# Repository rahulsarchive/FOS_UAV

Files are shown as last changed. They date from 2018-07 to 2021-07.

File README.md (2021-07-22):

# FOS_UAV

The aim of this project is to develop an open source aerial mapping platform using standard hardware and to develop a workflow from data acquisition to data processing. 

open uav

FOS UAV is part of the Drone Research Program by [ICFOSS](https://icfoss.in/) (International Center for Free and Open Source Software)

## Overview

Most UAV's today are multirotors, they have the advantage of being able to hover and carry more payload like sensors and other auxilaries. But with the current battery technology, multirotors have a flight time in the range of 15- 20 mins, without compromising on the payload. They make good inspection drones in tight spots and hard to reach places. But because of the way they fly, they brun through a lot of  power, hence limiting the flight time and maximum range.

Fixed winged aircrafts fly on the principle of aerodynamic lift and are far more efficient at covering ground than multirotors. Even though they are considerably harder to design and build, they make up for with efficiency.

Our goal is to build a suitable fixed wing platform that can carry the necessary payload and provide usable data for arieal mapping. The craft needs to carry a good GPS system, a downward facing camera for taking images, and be able to fly missions autonomysly.

Our constrains being, it must be simple to make, and easy to use. All the hardware and software are low cost and open-source, without sacrificing saftey and usability.

## Related projects
 [**4-Axis Hotwire Foam Cutter**](https://github.com/rahulsarchive/4AxisFoamCutter)  
 [**CNC Drag knife**](https://github.com/rahulsarchive/cncdragknife)  

# Mapping Process
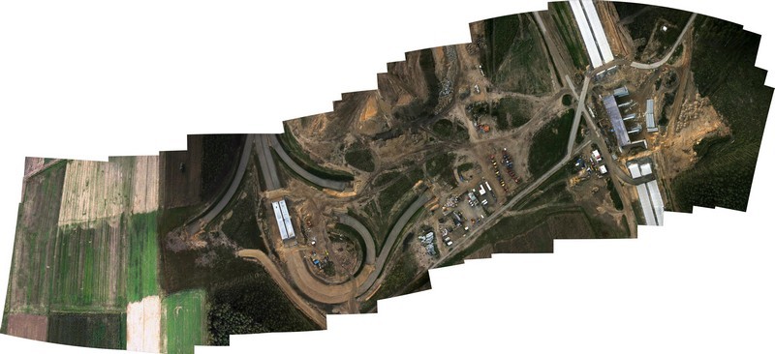
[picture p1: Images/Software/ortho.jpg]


The mapping is done by a process called **Photogrametry.** The UAV carries a camera which is angled down to take photos of the ground when the crafts flies overhead. The UAV then flies along a defined GPS way-point mission which covers the area to be apped with sufficient overlap. A software then reads all the images and then stiches them into an 3 dimensional orthomosaic.

Multiple data can be infered from the orthomosaic like, ground elevation, water level, cubic volume of materials. With suffient overlap and good camera altitudes, centimeter level accuracy can be obtained. But inorder for the process to work, the UAV must provide reasonably stable data over the entire course of the mission.

# Software

## Ardupilot
open uav

Ardupilot is one of the most advanced open source autopilot solution, it has been there the longest and has an active community developing it. The firmware support a wide range of vechiles from airborne to terrestrial and even underwater. It is paired with a suitable ground control software to bring out is full functionalities.

In the latest release of Ardupilot they moved onto the Chibios platform and have now extended support for some of the common STM32 F4 flight controllers like the Omnibus F4 and the Matek F405 wing. We will be using this version and testing the features, the new firmware is still in beta and being actively developed.

## INAV
open uav

Inav is a flight control software, which was forked from Clean Flight. The software supports both multi-rotors and fixed wings and has good GPS modes like Return to launch (RTH) etc. The software has a mission planner, which allows for setting full autopilot GPS way-point navigation. It supports a variety of Flight controller boards and is actively being developed by the community.

## OpenDroneMap

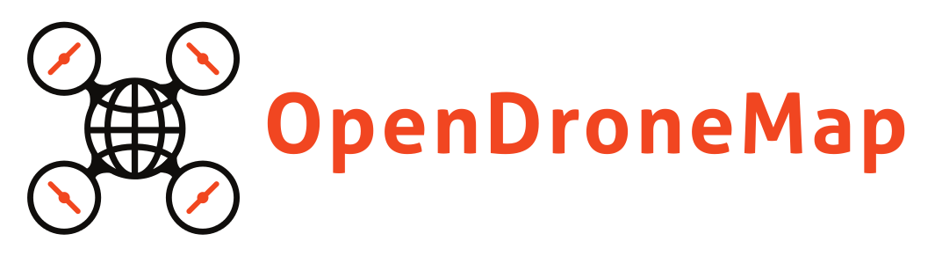
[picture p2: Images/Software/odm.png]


OpenDroneMap is an open source toolkit for processing aerial drone imagery. OpenDroneMap turns the images captures by the drone into three dimensional geographic data that can be used in combination with other geographic datasets.

it can process a collection of images into point clouds, Digital surface models, Digital Elevation Models etc.

## Mission planner

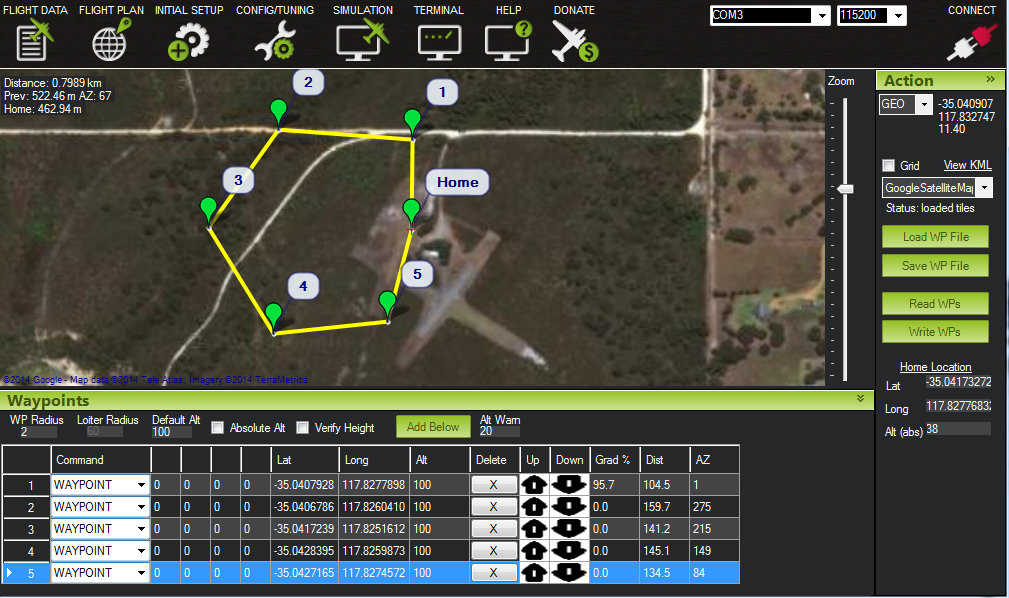
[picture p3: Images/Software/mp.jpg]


Mission Planner is a ground control station for Plane, Copter and Rover. It can be used as a configuration utility or as a dynamic control supplement for your autonomous vehicle. It can be used to configure and tune your vehicle, plan and load autonomus gps way-point missions. With proper telemetry hardware, it can provide the live status of the vehicle, record telemetry data and operate the vehicle in FPV (first person view)

# Hardware

## Design consideration

The flight characteristics need to be kept in mind when choosing an aircraft. We wanted to keep thing simple, and minimze the number of moving components. Hence no tail. The aircraft will be a flying wing,simple and monolithic in construction, good performance and agility.

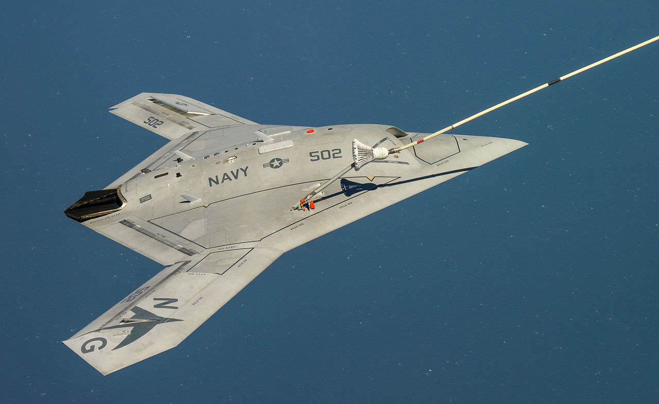
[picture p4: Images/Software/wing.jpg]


### Wing Aerodynamics 101

The two most important parameters when desiging an aircraft are the **Center of Gravity (COG)** and the **Center of Pressure (COP)**. The COG is the point where the weight of the aircraft acts and the COP is the point where the aerodynamic lift forces act. For the plane to be  stable, the COG must be in front of the COP. But this means the airplane has a tendency to nose down when flying. Thats where the tail comes in, the tail on a conventional airplane is set at a slightly downward angle compared to the wing, a term known as Decolage.

So the wing is lifting up and the tail is pushing down to keep the plane stable. If the COG is too far forward the wing has to push down even more and the wing has to make more lift to counter this effect. The inverse is also true, if the COG is too far back then the tail has to push up to keep the plane level, this is not a stable condition and its very difficult to fly a tail-heavy plane.

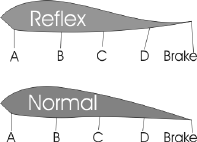
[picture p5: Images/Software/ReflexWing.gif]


A wing emulates a stable flying conditon by having a forward COG and using its Elevons (Elevator+ Aeilerons) to pitch the wing up, A term known as **Reflex** in which the elevons are kept at a slight up to push the tail down and pitch up the wing. This is not without consequences, the more forward the COG the more the elevons have to pitch up, there by creating more induced drag. The next parameter which influences the COG and hence the stability is the **Sweep Angle**.

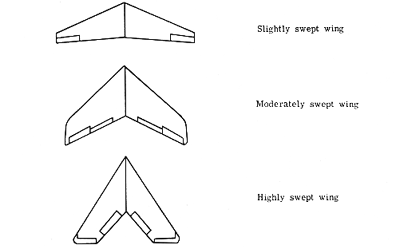
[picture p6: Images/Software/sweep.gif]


 Sweep is importart because it provides leverage for the COG to act. The COG needs to be at about 25-30% of the chord, in a rectangular wing, this is very close to the leading edge and will not provide enough leverage to balance the COG, so we need a long fuselage in front of the wing to carry the weight.

In a wing, the CG needs to be at about 20-30% of the **Mean aerodynamic chord**, whcih takes into account the root and tip chord and the sweep angle. In simple terms, the more the sweep, the farther back the COG can be and the more leverage you can get. But the more the sweep the less the lift is produces per wingspan. Sweep also has another effect, it acts like a **Dihedral**

A **Dihedaral** is a slight angle between the wings to provide stability. When one wing dips, it produces more lift than the other wing and the aircraft comes back to level. A side effect being, it will cause the wing to wobble, as the side facing the wind will have more lift than the trailing wing.

Flying wings are a lot harder to control as they are inherently unstable aircrafts. They are very sensitive to the changes in Center of Gravity (CG) and flying them manually is a skill.

Since our objective is to get stable data, flying them manually is not an option. This is where a flight controller comes in, it will keep the craft stable and provide additional features.

### Choosing an Airfoil 

In our version #2 build, we used the Clark y airfoil for the wing but it did not perform as well as we expected, after a bit of research on tip stalling and how to avoid it in a wing, we stumbled upon the **KFm airfoils**. On paper they seemed very good, so we decided to try them out.

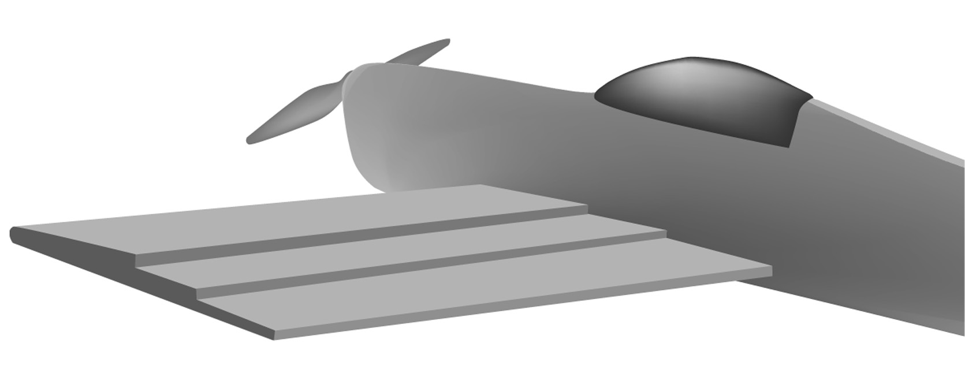
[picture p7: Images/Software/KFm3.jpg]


The KF stands for Kline and Foggleman who were the designers of the KF airfoils. Unlike a conventional smooth airfoil. The KFm airfoil uses a series of layers to create stepped airfoils.

There are a number of KF variations, That use a combination of layers and positioning to produce a wing that can be made to emulate what a normal wing airfoil profiles.

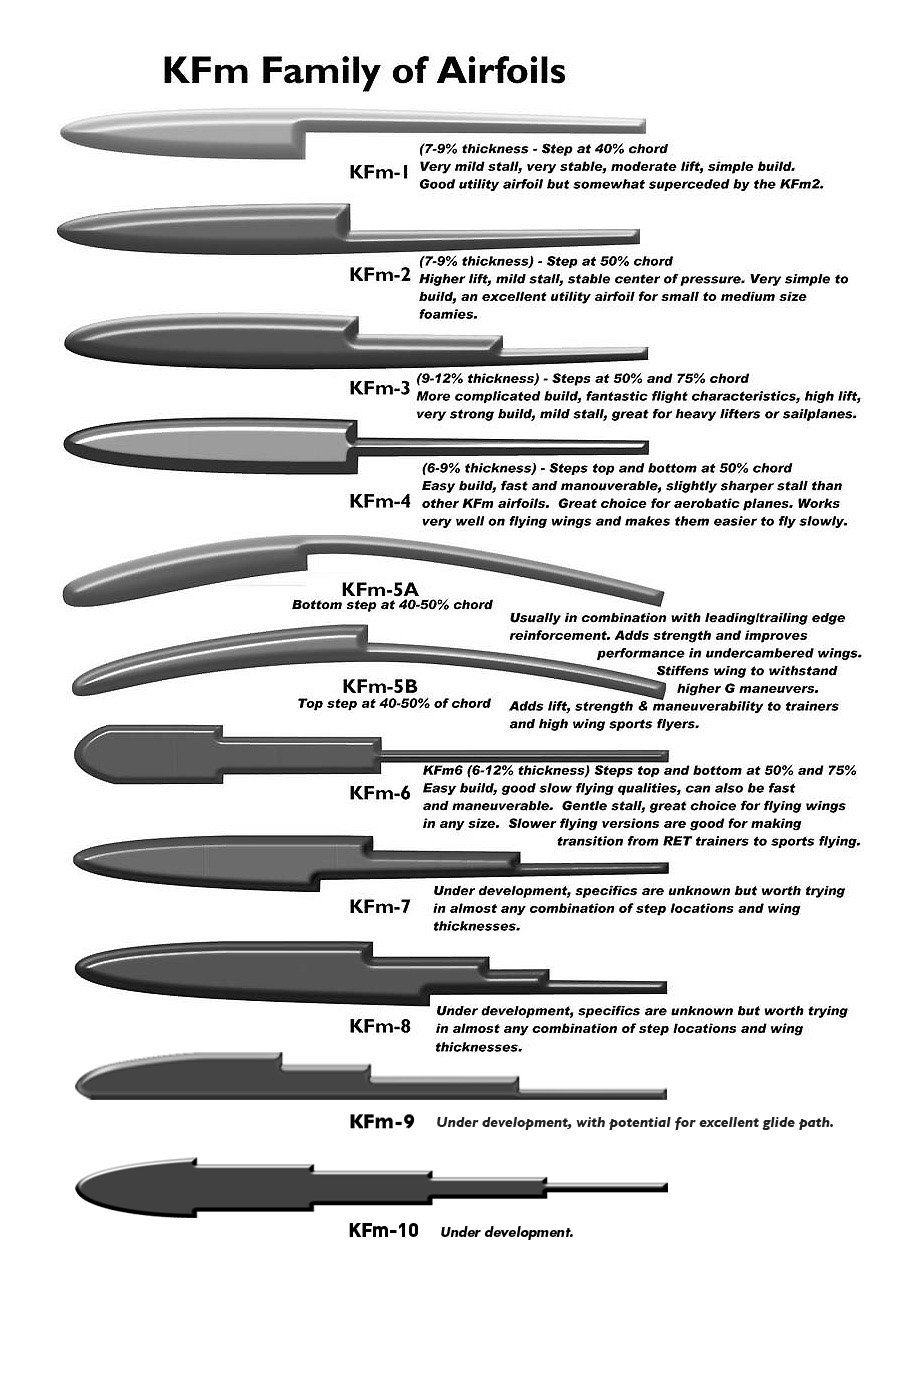
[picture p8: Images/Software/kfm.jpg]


Drawn up by Dick Kline these give some basic guide numbers  for the various combinations that have been tried. The guide numbers however are open to changes, going thinner will always work, going a bit thicker will often work, go too thick and it wont work. 

The percentage thickness refers to each sections total thickness vs the total chord of the wing, and not the height of the step. The height of the step is only determined by the thickness of your foam sheet. Steps can be raised to give more height and the step effect increases proportionaly with both height and air speed.

The basic stepped airfoil idea is that there will be a vortex produced behind each step that fills in the gap and lets the air flow over over the wing as though  the gap was solid and profiled.

For more details, check the RCgroups form on KFm theory and science.

[Kline-Fogleman-(KFm) Airfoils Advanced Theory Science](https://www.rcgroups.com/forums/showthread.php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**)

#### Some positive characteristics of KFm airfoils

1. It can handle a wide range of speeds form very slow to fast.  
2. It has much greater range for its center of gravity, it could be moved as much as 40% back, since the entire rear section of the wing is producing lift.  
3. It has very good stall characterisitcs and it retards tip stalling in a flying wing.  

### Power plant selection
	
The power plant in an electric aircraft is not just the Motor alone, but a combination of Motor, Propeller, and the battery. The battery can be thought of as both the energy source and the supercharger. When a motor is under load, it will pull a lot of amps, and the battery must be capable of supplying it.

Batteries are rated for their capacity and discharge rating. The capacity is the totoal amount of charge it can hold, bigger mAh gives longer flight times, but are also heavy. The discharge rating, denoted by 'C rating' is the max amount of current it can deliver at a time.

**Max current from battery = mAh x C rating.**

Select good batteries with high discharge rating, so that it can keep up with the motor.

The motors are rated in watts for the amount of power they deliver. Now how they deliver that power depends on the motor specifications namely,

1. Higher Kv motor spin faster, use smaller propellers, consumes a lot of current and are generally used for high speed aircraft.  
2. Lower Kv motor spin slower, use large propeller, produce lots of thrust, consumes less current, Generally used for larger planes with big props.  
3. The numbers on the motors generally indicate the size of the stator eg - 2212 1000kv motor, means stator dia is 22 mm and height is 12 mm.  
4. Larger diameter motors produce more thrust. Taller motors are stable at higher speeds.  

The propeller converts the mechanical energy from the motor into thrust. They are specified by their diameter and pitch. A "5X4 prop" has 5 inch diamter and 4 inch pitch. 

Generally,

1. Larger props produce more thrust, smaller props are more responsive.  
2. Always match motor to propeller. Lower Kv pairs with larger props and vice versa.    
3. For efficiency, go for the larges prop you can fit on the aircraft.  
4. Larger props produce more thrust, higher pitch gives faster speed.

### Flight controller

A Flight controller is basically an inertial measurement unit (IMU) plus a couple of sensors and a processor to read the sensors and act on the motors. It is constantly monitoring the orientation of the craft and trying to keep it level against outside disturbances. Most flight controller can run software which provides a host of abilities like GPS navigation, Auto-land/take-off etc.

There are a many open-source flight controllers designed for fixed wing like the **APM** and **Pixhawk**. But we can use the mini race quad boom to get cheap and efficient flight controllers.

Most mini quads today use a flightcontroller which has an STM32 chip on it, depending on the performance required, they range from F1 to F7 series. we settled on an **STM32F4 flight controller** which is a happy medium between performance and the number of devices that can be connected to it.

The flight controller needs software to run. There are couple of opensource softwares to choose from like Ardupilot, Betaflight, Cleanflight, INAV etc. Most softwares are geared towards multirotors but there are a few which support fixed wing crafts.

We chose Ardupilot as the flight control software as it met all the requirements and has good mission planning capabilities.

## Hardware 

The hardware is low cost and reliable, and can be obtained off-the-shellf

### Bill of Materials

| Sl No | Item | Description | Qty |
| --- | --- | --- | :--: |
| 1.	| **Matek F405 wing** | STM32F405 Flight Controller | **1** |
| 2.	| **Beitian BN-880 GPS module** | GPS Receiver | **1** |
| 3.	| **DYS D3536  1400KV** | 1000Kv 700W motor | **1** |
| 4.	| **SkyWalker 60A Esc** | 60A ESC | **1** |
| 5.	| **Towerpro MG90S Servo** | 9g Metal Gear Servo | **2** |
| 6.	| **Pushrod connectors** | Servo pushrod connectors | **2** |
| 7.	| **Gemfan 9X6 Prop** | 9X6 prop | **1** |
| 8.	| **Tattu 5000mAh 30C** | Lipo Battery | **1** |
| 9.	| **Frsky S8R Receiver** | Frsky Telemetry receiver | **1** |
| 10.	| **Sik Telemetry Radio 433Mhx** | Dual-way Telemetry Radio | **1** |
| 11.	| **5mm Depron Sheet** | 5mm XPS Sheet | **10** |

### All previous design iterations can be found on the [Build Log](https://github.com/rahulsarchive/FOS_UAV/tree/master/Build%20Log)

## Version 4.0 (Stingray, KFM6)

**Wingspan: 1250mmm   
Sweep: 30 deg  
Root chord: 380mm  
Tip chord: 220mm  
AUW: 1300g  
Power plant: 3536 1400kv motor (9X6 prop)** 

The design of the wing was influenced by our previous iteration (Tomcat), depron is good material for construction. The current model is designed to carry a lot more weight than its predecessors, hence the sweep angle is reduced to 30 deg to account for the change in center of gravity.

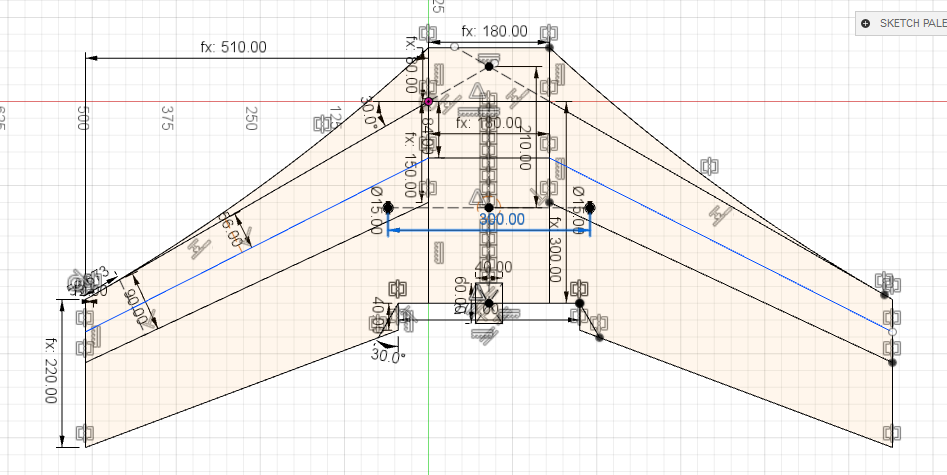
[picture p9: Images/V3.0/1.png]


The wing is made by stacking the depron sheets on top of each other and glued together. This allows for rapid prototyping and repair in case of a crash. The design can be cut by hand with a ruler and knife, there is very little curves to cut.

For ease of fabrication we exported the design as 2D profiles and cut them out on Shopbot 3-axis mill.

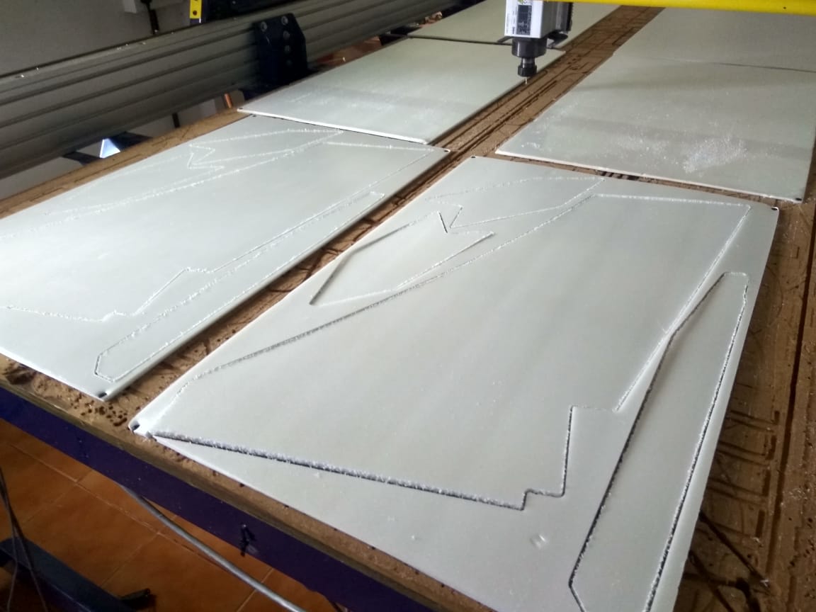
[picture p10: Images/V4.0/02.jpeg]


The parts are easy to fit together and designed in a way to prevent concentration of stress points (Glue joints) at a single place. The two base pieces provide a foundation on which rest of the pieces are stuck. The joint is reinforced by top plates and the KFm airfoils are stuck on top.

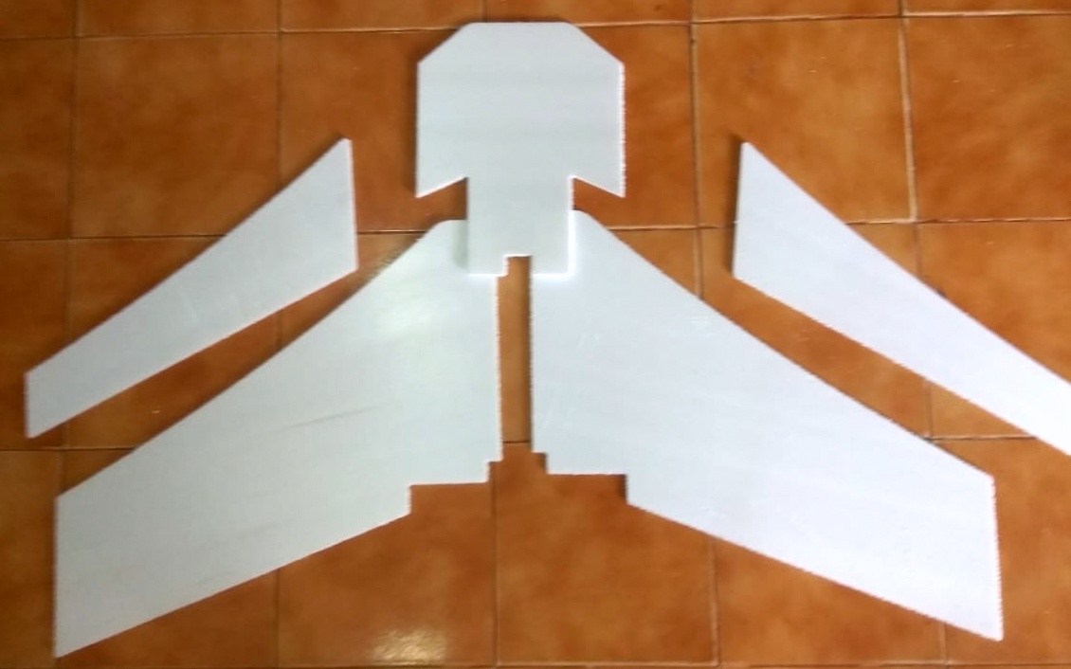
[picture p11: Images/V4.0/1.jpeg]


The arrangement provide a easy and rugged frame for the wing.

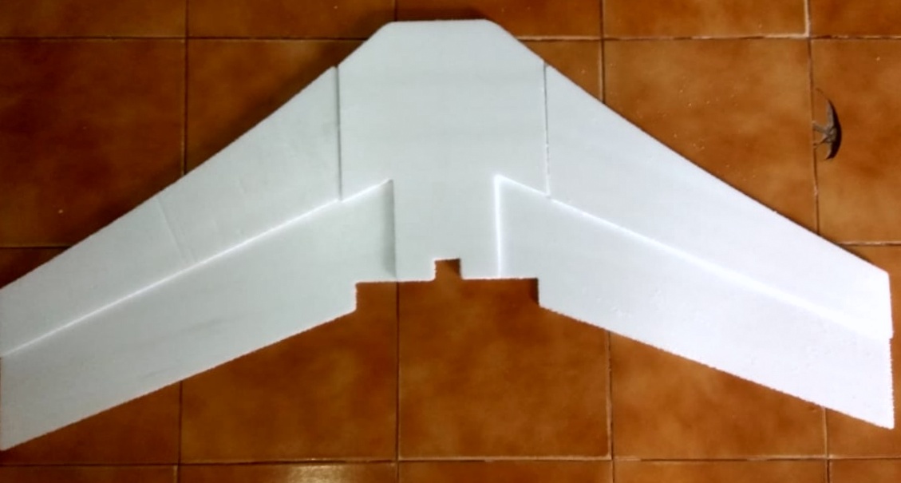
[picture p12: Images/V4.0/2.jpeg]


All the pieces are stuck together with syntetic resin adhesive, a polyurethane glue like Uhu Por is recommended. Sticking the parts together is simple and provides a strong bond, which prevents bending.

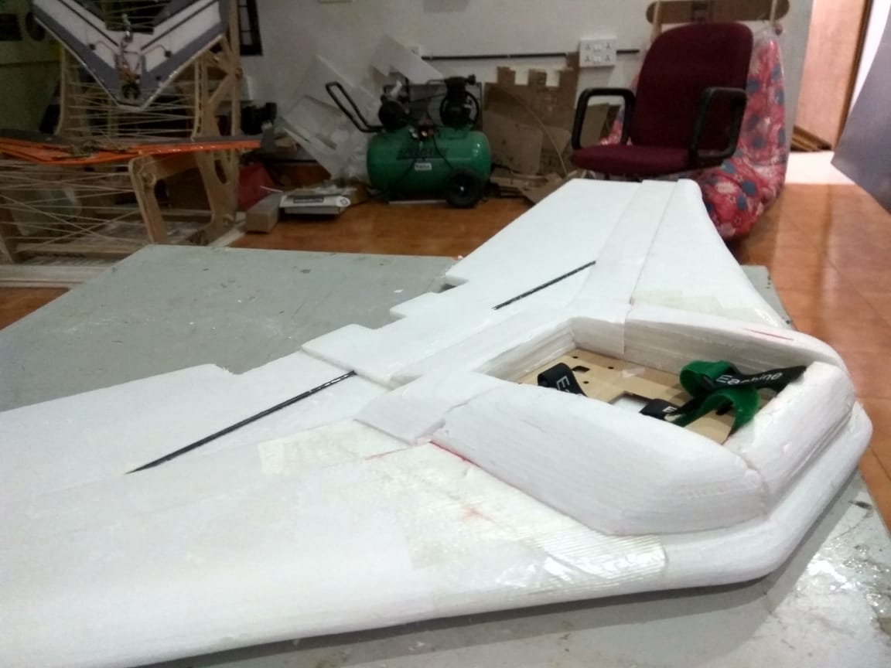
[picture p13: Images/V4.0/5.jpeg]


The Elevons sanded to give an airfoil shape and attached to body uing Nylon hinges. The Nylon hinges provide a smooth travel of the elevons.

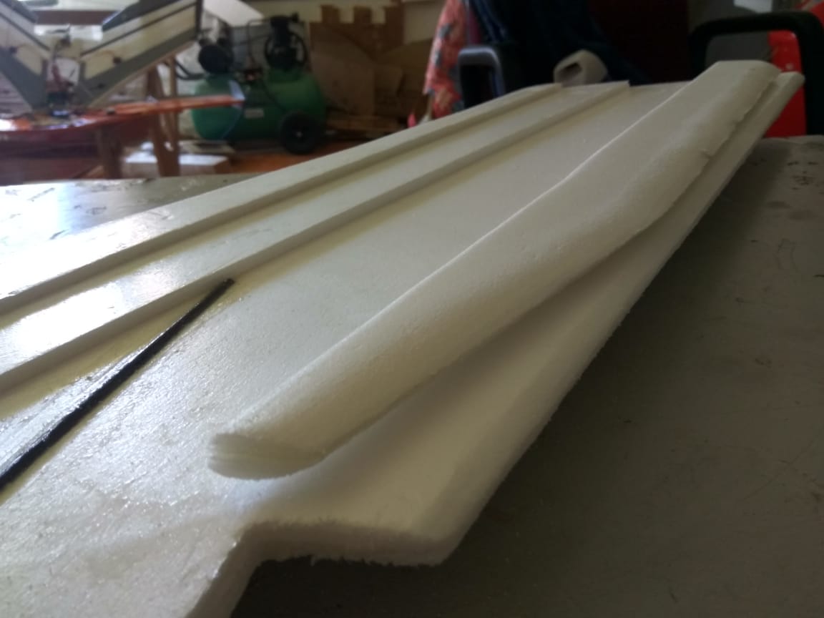
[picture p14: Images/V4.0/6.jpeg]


The airframe is finished by spray painting and covering it with a layer of tape. The tape provides tensile strength to the body and acts a protective outer shell. Strieps added for visual effect!

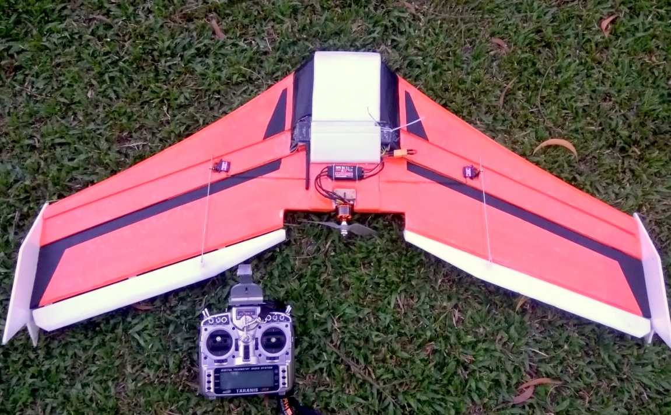
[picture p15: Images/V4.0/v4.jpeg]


The wing flies well, it needs a 5000mah battery and a Gopro camera in front to balance out the CG but once its balanced, it flies like on rails, good glide slope and stall characteristics. The KFm6 seems to work well with this air frame.

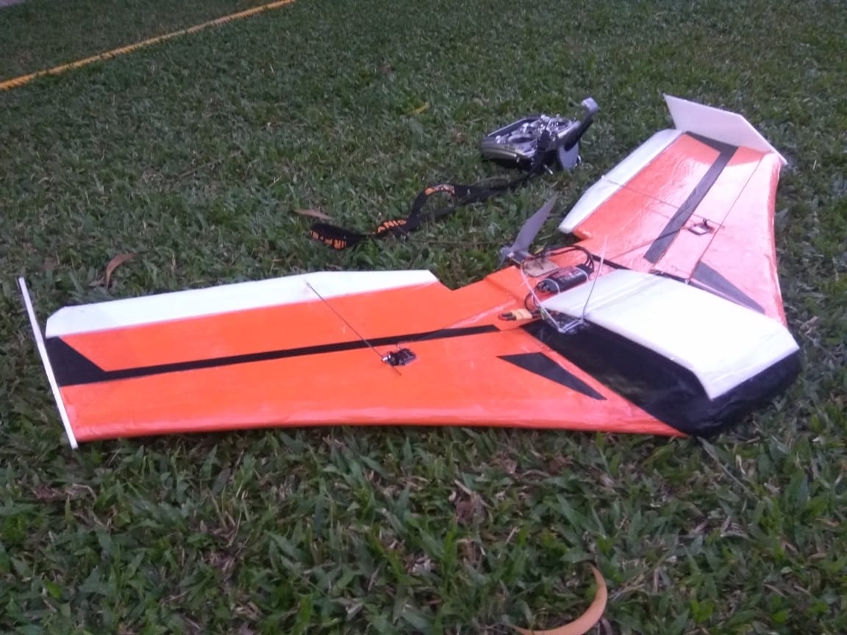
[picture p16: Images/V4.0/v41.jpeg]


### Flight Test

FOS_UAV (https://www.youtube.com/watch?v=VQGO6bCqtgY)

## Version 5.0 VTOL Tailsitter 

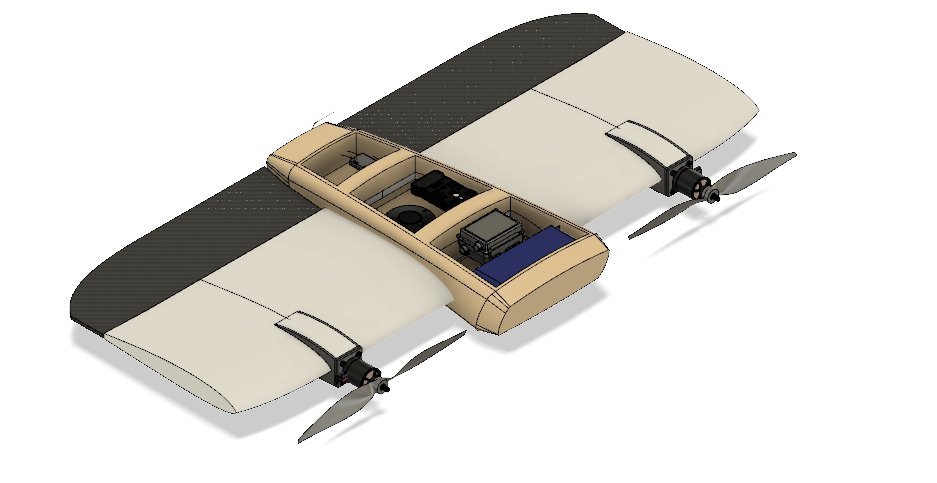
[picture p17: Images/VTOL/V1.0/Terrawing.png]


A 1m wingspan 2.5Kg AUW Vertical take-off and landing Tail-sitter aircraft.

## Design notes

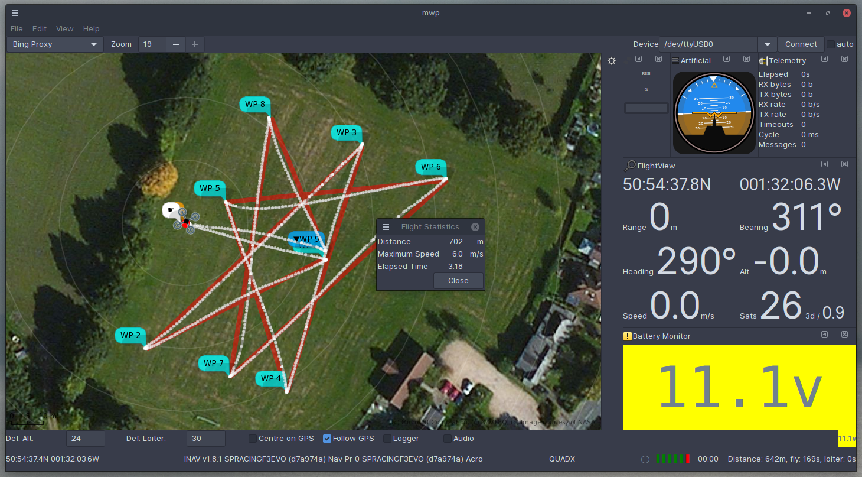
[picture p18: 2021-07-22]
Images/Software/mwp.png

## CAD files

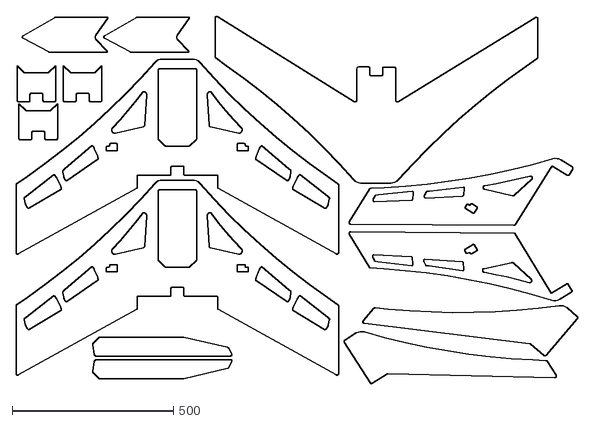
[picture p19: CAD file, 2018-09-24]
Design Files/Albatross V2.0/Albatross.dxf
1741.6 x 1138.4

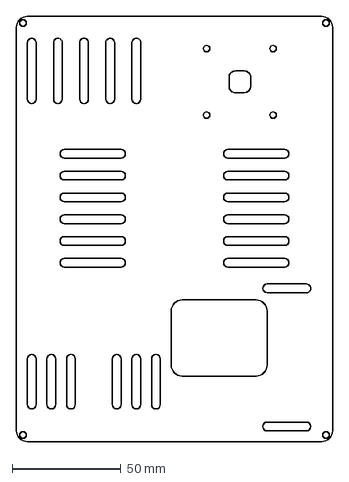
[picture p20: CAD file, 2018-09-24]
Design Files/Orange Fury V3.0/batplate.dxf
145.0 x 195.0 mm

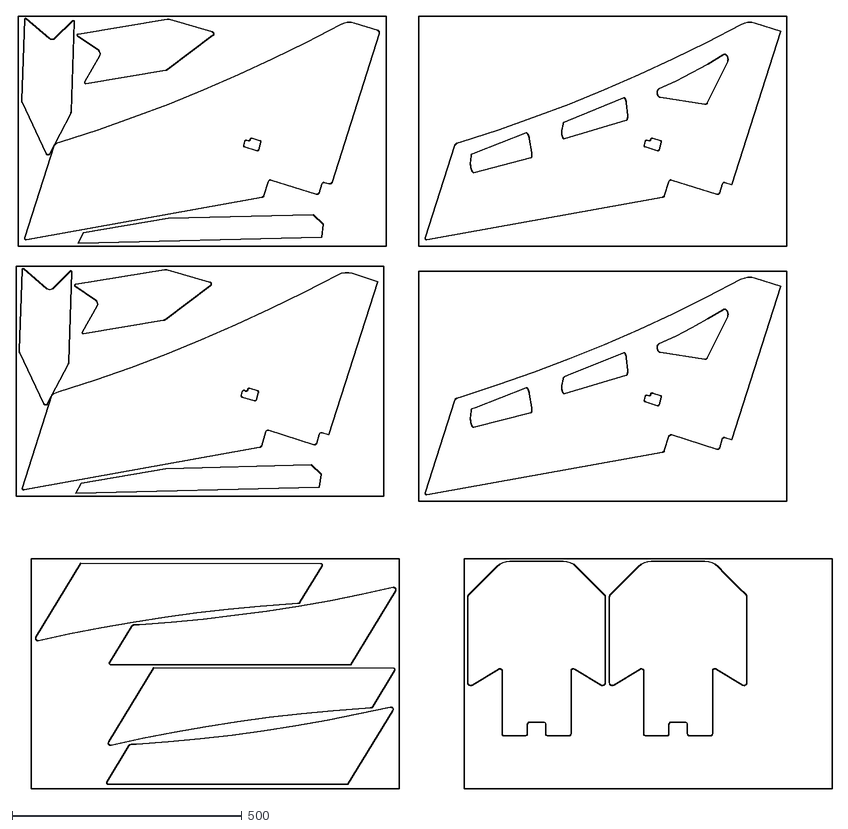
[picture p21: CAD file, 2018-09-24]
Design Files/Tomcat V2.1/Tomcat.dxf
1774.5 x 1680.3

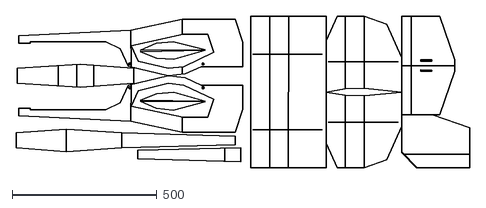
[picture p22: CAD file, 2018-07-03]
Design Files/Trainer V0.5/Trainer.dxf
1565.9 x 521.8

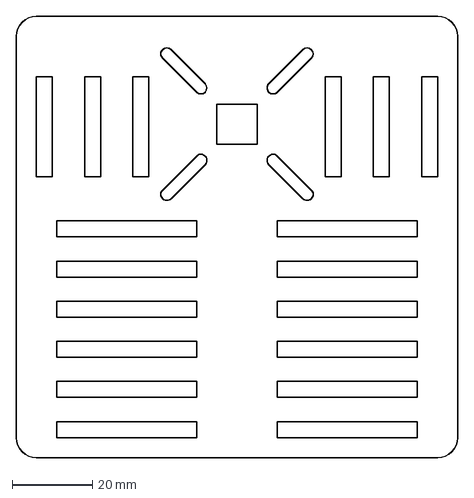
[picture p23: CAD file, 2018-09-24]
Design Files/Albatross V2.0/batplate.dxf
110.0 x 110.0 mm

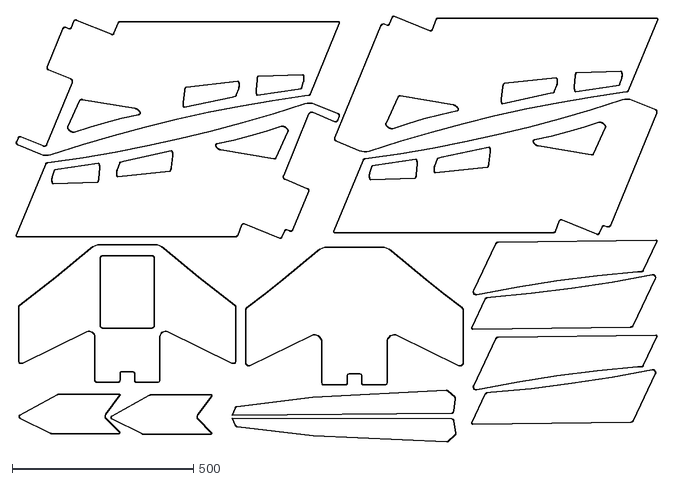
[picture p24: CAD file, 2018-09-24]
Design Files/Orange Fury V3.0/Orangefury.dxf
1770.4 x 1175.5

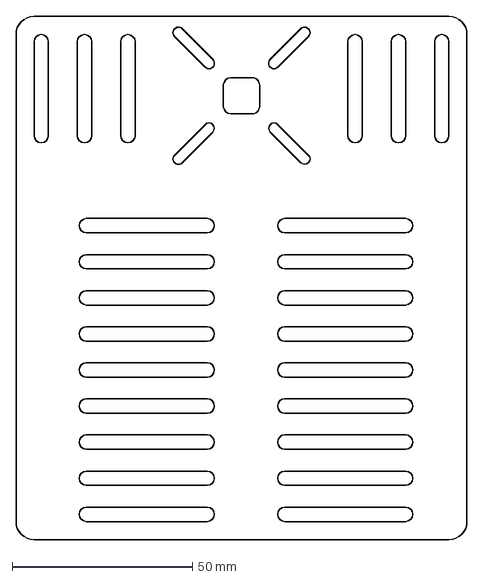
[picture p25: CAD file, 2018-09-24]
Design Files/Tomcat V2.1/battplate.dxf
125.0 x 145.0 mm

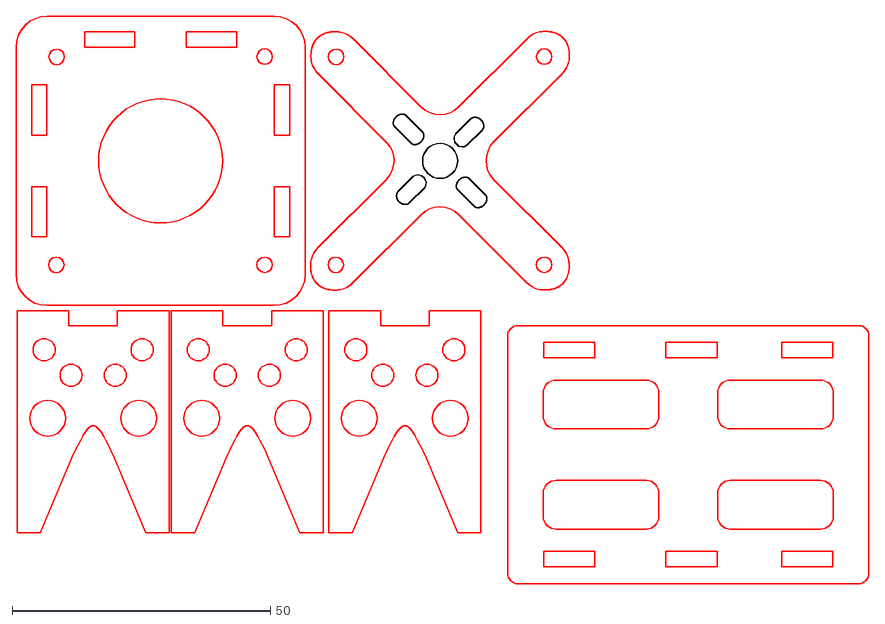
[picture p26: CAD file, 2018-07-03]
Design Files/Trainer V0.5/Motor mount.dxf
165.2 x 109.9

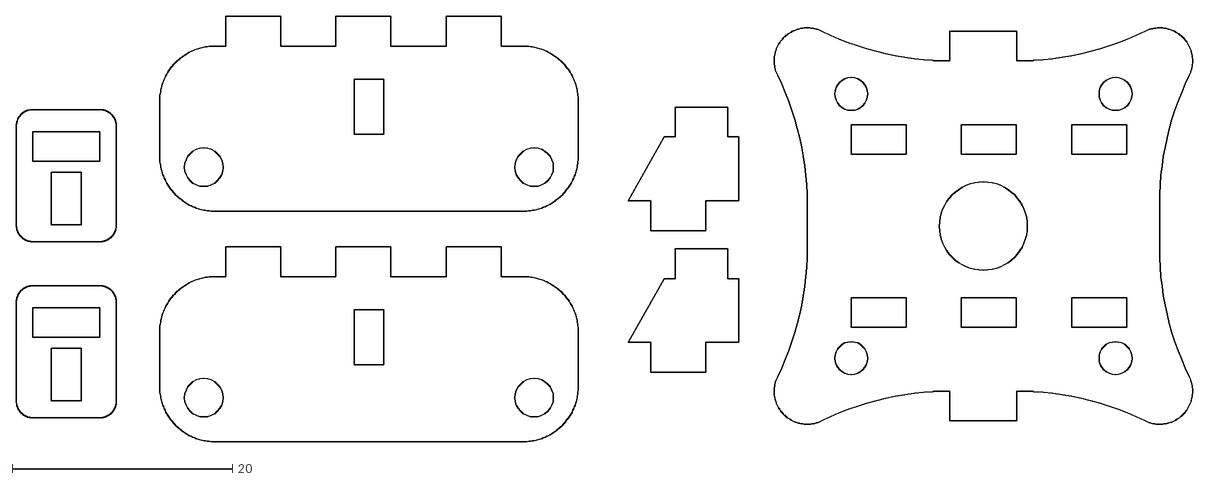
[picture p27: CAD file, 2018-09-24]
Design Files/Albatross V2.0/2.7mm motor mount.dxf
106.8 x 38.6

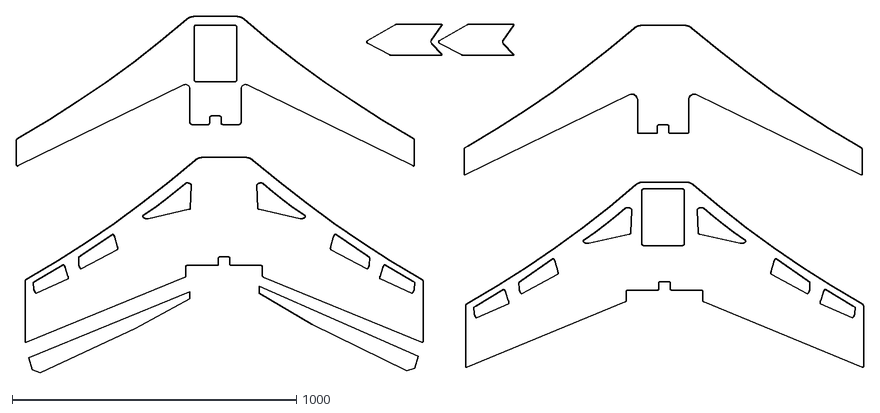
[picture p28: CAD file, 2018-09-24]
Design Files/Orange Fury V3.0/1.4m kfm4.dxf
2979.5 x 1252.3

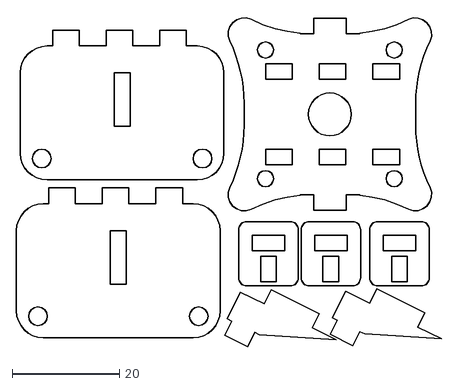
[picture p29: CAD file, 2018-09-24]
Design Files/Tomcat V2.1/Motor Mount.dxf
79.3 x 61.6

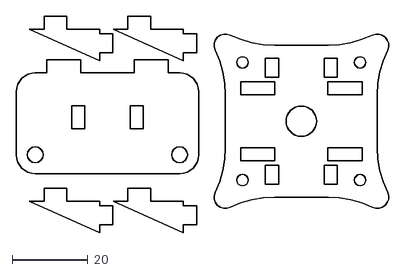
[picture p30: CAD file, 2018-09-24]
Design Files/Orange Fury V3.0/Motorplate.dxf
98.3 x 57.0

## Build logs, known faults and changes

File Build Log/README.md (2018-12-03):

# Build Log

This is the log of our design and iteration process, it details the things we did and what we learned from them.

## Version 1.0 (Phenoix, Cark Y foam wing)

Wingspan: 800mm  
Sweep: 30 deg  
AUW: 870g  
Power plant: 2212 1000kv motor (10x4.7 prop)  

This is our first attempt at making a flying wing. This wing will be made from styrofoam and since a hot wire cutter is the most efficient way to cut foam, we decided to built a [4-axis CNC hotwire cutter](https://github.com/rahulsarchive/4AxisFoamCutter) to help us make the wing cores. Its been a blast making it, see the repo for the documentation.
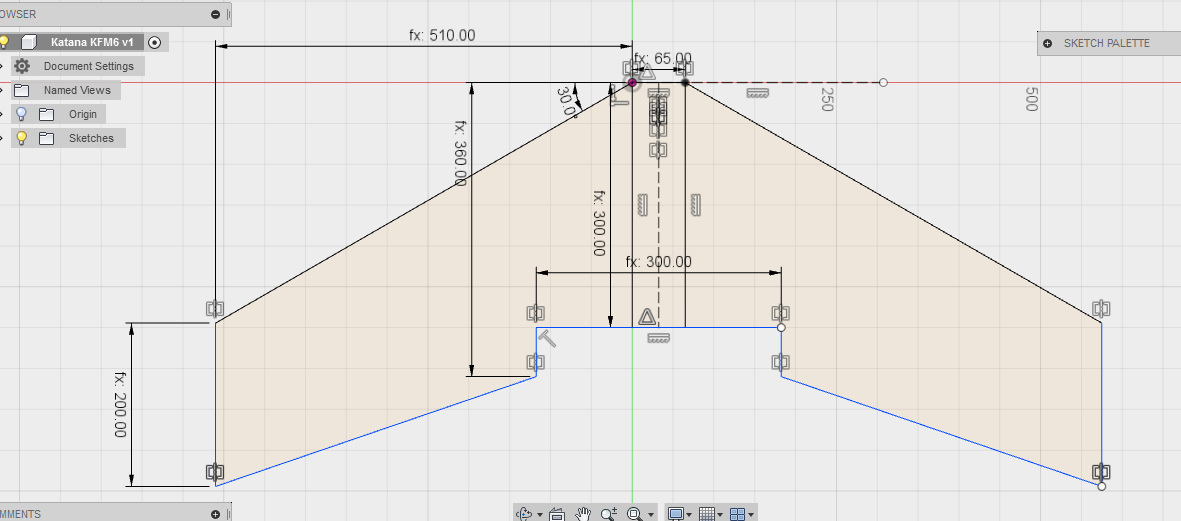
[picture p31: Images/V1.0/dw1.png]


After a bit of reasearch on fying wings, we settled on the parameters and started working on the design.The wing will have a wingspan of 800mm, swept back at and angle of 30deg and have a blunt nose fuselange in between to carry all the payload. The hot wire cutter helped us tremendousely in cutting out the wing cores. 

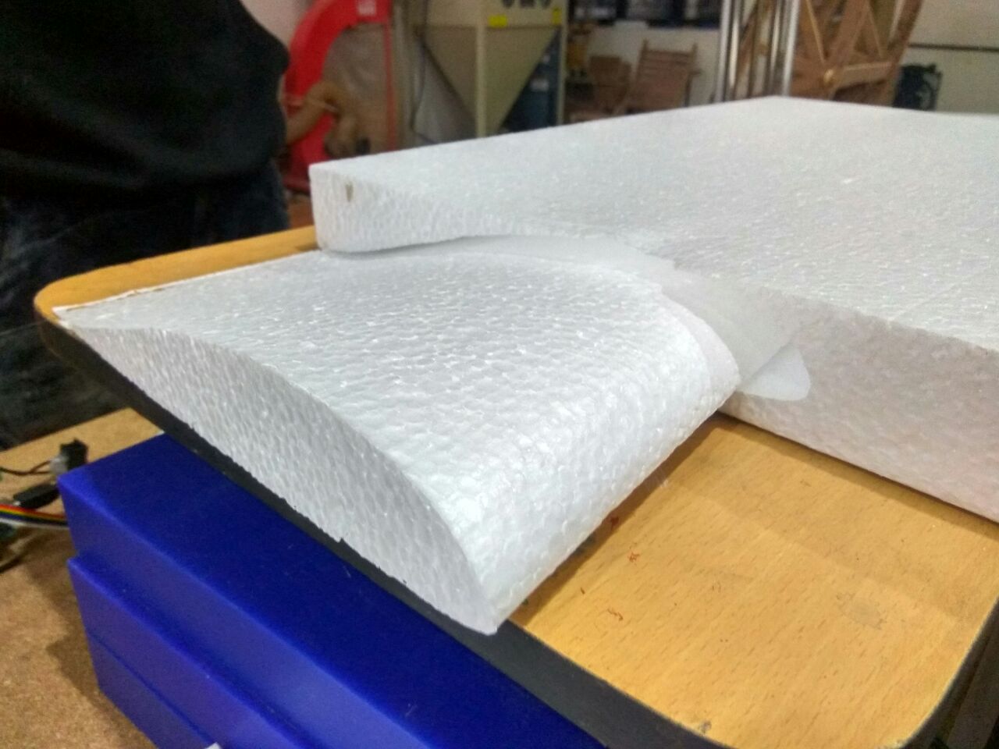
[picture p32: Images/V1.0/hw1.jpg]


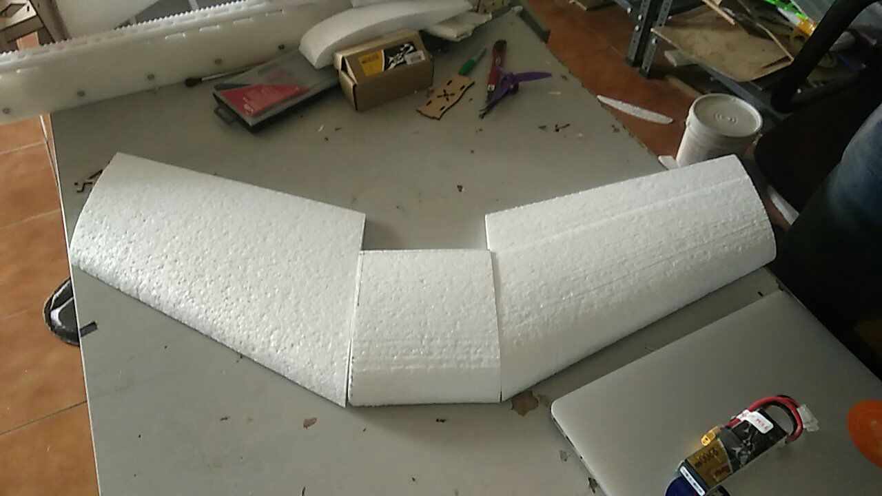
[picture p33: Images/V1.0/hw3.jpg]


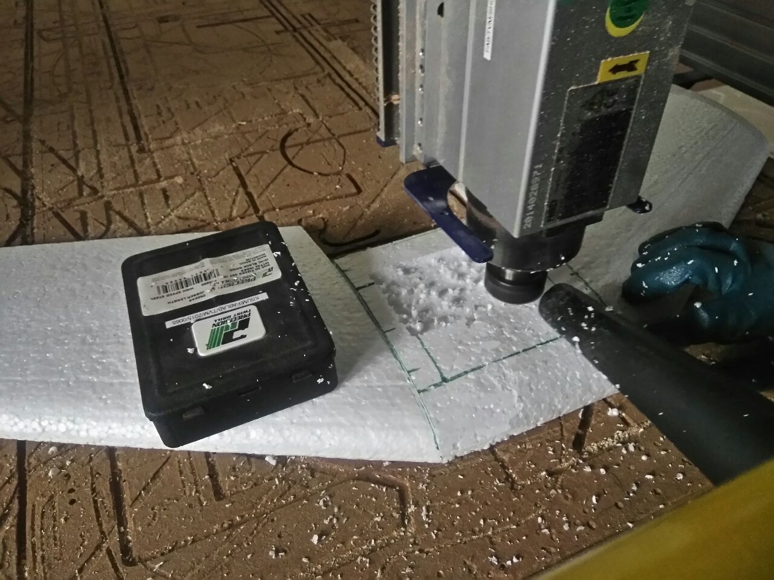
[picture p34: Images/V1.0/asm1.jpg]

For additional strenght we decided to do a composite on the wing cores with wood glue and paper towels. This gave us a hard and rigid outer shell which can take the impact of landings. This shell was coverd with a layer of packing tape to seal all the rough edges and then a layer of vinyl tape to provide some colour.

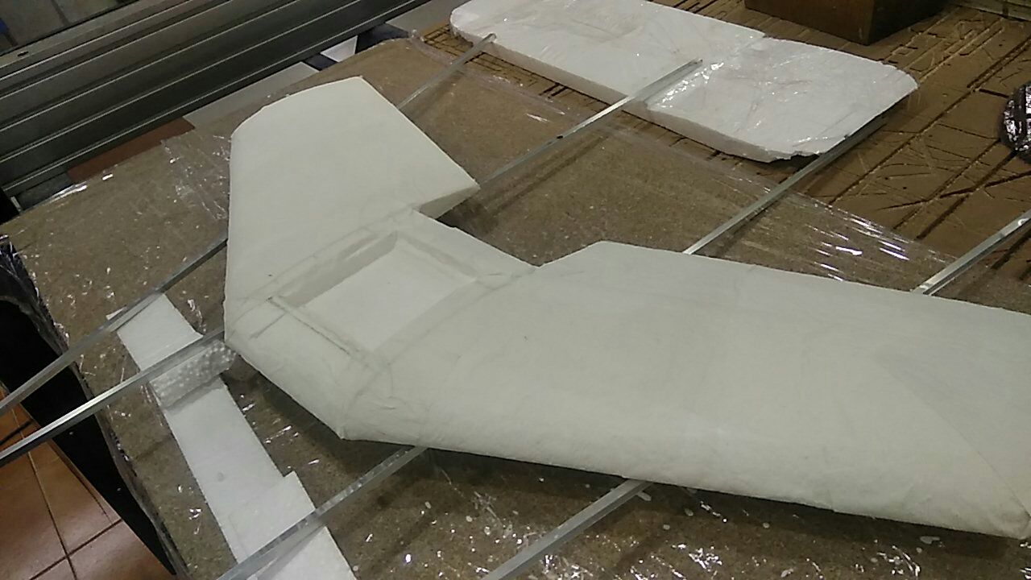
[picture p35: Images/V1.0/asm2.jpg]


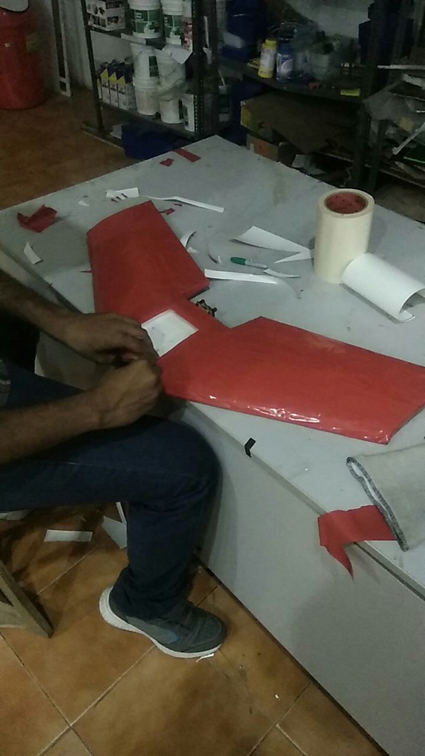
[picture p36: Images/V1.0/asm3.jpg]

The wing is very light weight with the foam cores and has a tough shell to protect it in impacts. The motor mounts were laser cut on 3mm birch wood and joined to the wing with glue. Though originally desinged for a 2205 2600kv motor. In the end we had to go with a 2212 1000kv motor running a 10x4.7 prop.

We realized one problem when tried to balance the CG of the wing. There was not enough weight on the front to get the CG where we wanted, even with the bigger batttery the plane was still tail heavy. For the intial maiden we added bit of nose weight to bring the CG forward.

The maiden did not go successfully. It was very difficult to control and came down nose first. The wing was very heavy and barely had enough thrust to get it flying. Especially with all the drag from the large front bumpers. We realized that even though we designed for a 30deg sweep angle, after construction, the sweep was around 24deg. This pused the CG point forward and there was not enough weight in the front to balance it.

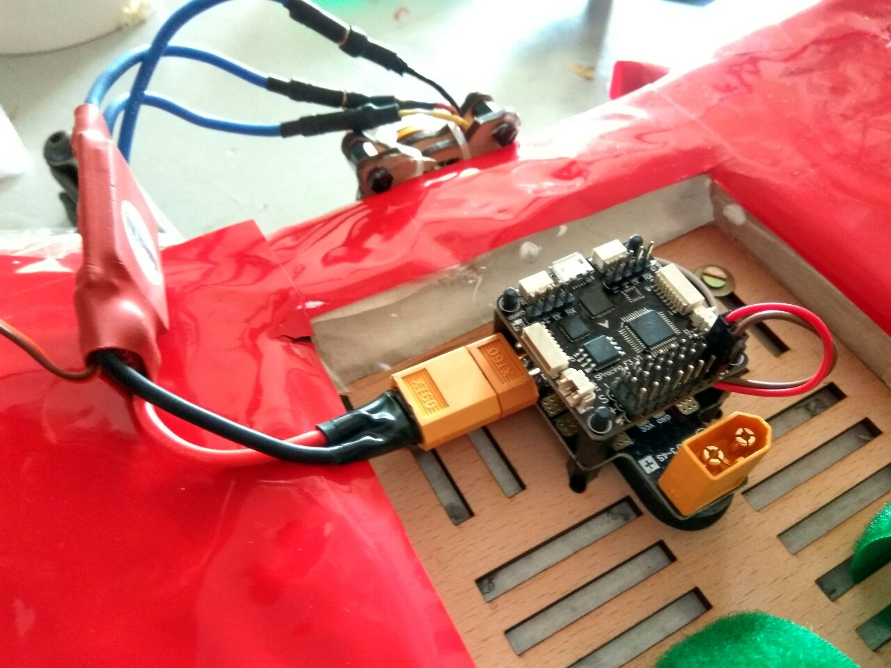
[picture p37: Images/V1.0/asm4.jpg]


we tried putting a flight controller in it to help in stablizing the craft. We were able to fly with the help of flight controller. The model is still too tail heavy and the plane does not have enough thrust to carry the extra nose weight.
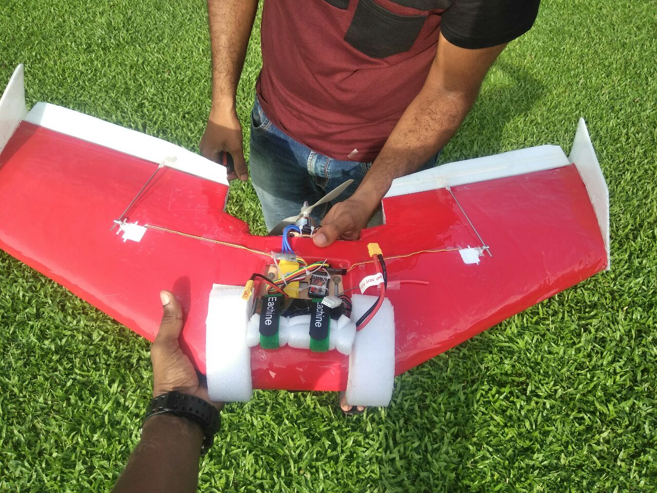
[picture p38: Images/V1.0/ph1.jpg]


### Note 

1. The single biggest factor that controls the characteristics of a flying wing is the CG.  
2. Wings are very sensitive in the pitch axis and sluggish in the roll axis.  
3. Manually flying them are hard, unless you have a lot of experience or very low wing loading.  
4. Adding a flight controller helps with stability and leveling the aircraft.  

## Version 1.5

This is our first version of our wing using a KFm6 airfoil. The center fuselage is designed to carry a camera, two 2500mah lipo, the flight controller and the motor. It needs to be strong to survive impacts and protect the electronics.

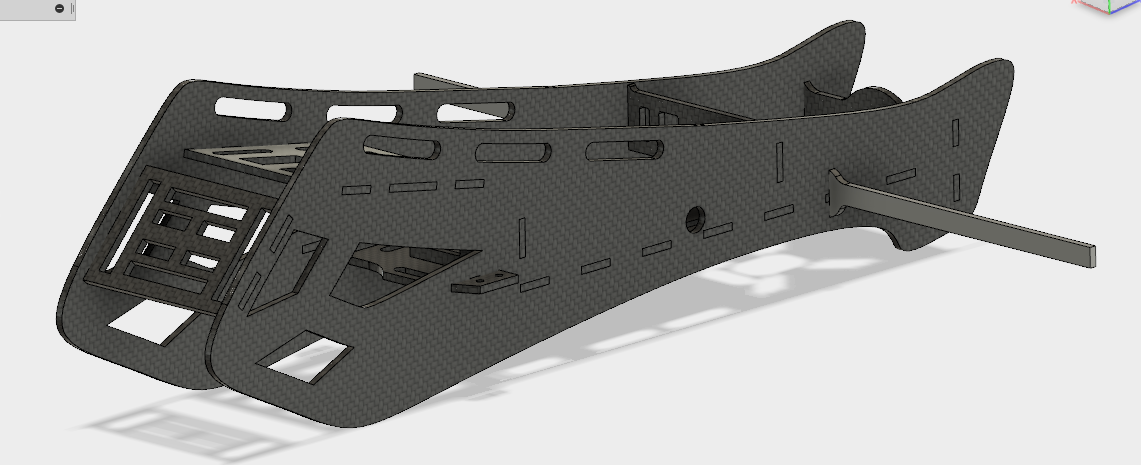
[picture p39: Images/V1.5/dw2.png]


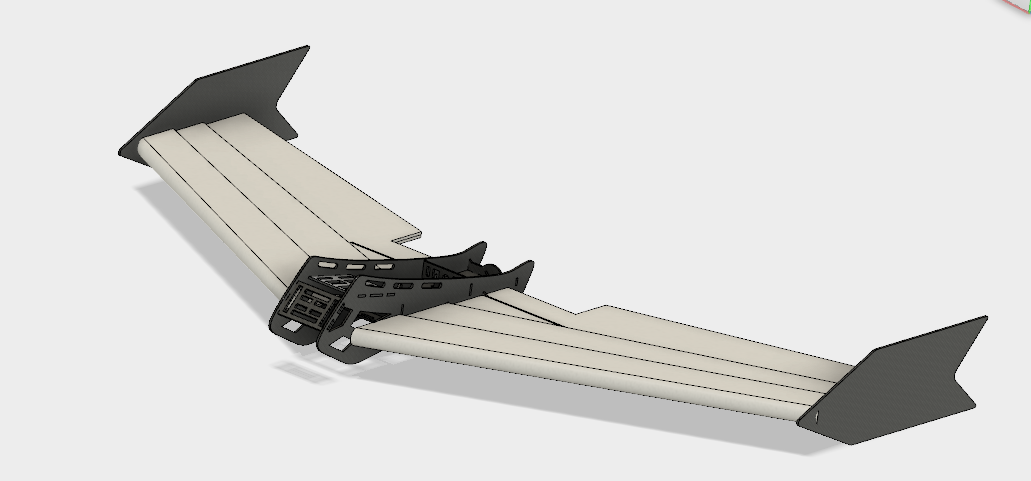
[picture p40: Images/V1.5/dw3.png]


We decided to keep this on hold until we test out the KFm airfoils on more simpler airframes. 

## Version 2.0 (Albatross, KFM6 wing)

Wingspan: 1000mmm   
Sweep: 35 deg  
root chord: 300mm
tip chord: 250mm
AUW: 1200g  
Power plant: 2826 1500kv motor (9X6 prop) 

Learning from our previous wing build, we decided to increase the sweep angle to 35 deg to push the COG backwards, so the wing would balace with less weight upfront. This wing will be an all foam construction and will accomodate a battery plate to house all the electronics.

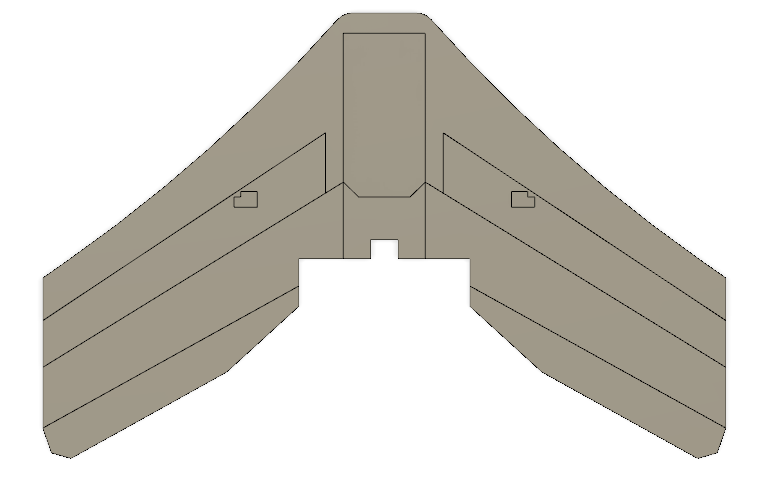
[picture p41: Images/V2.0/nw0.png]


The wing will have six layers in total, two base layers and two KFm steps on top and bottom. With all the extra foam, the construction will be heavy.

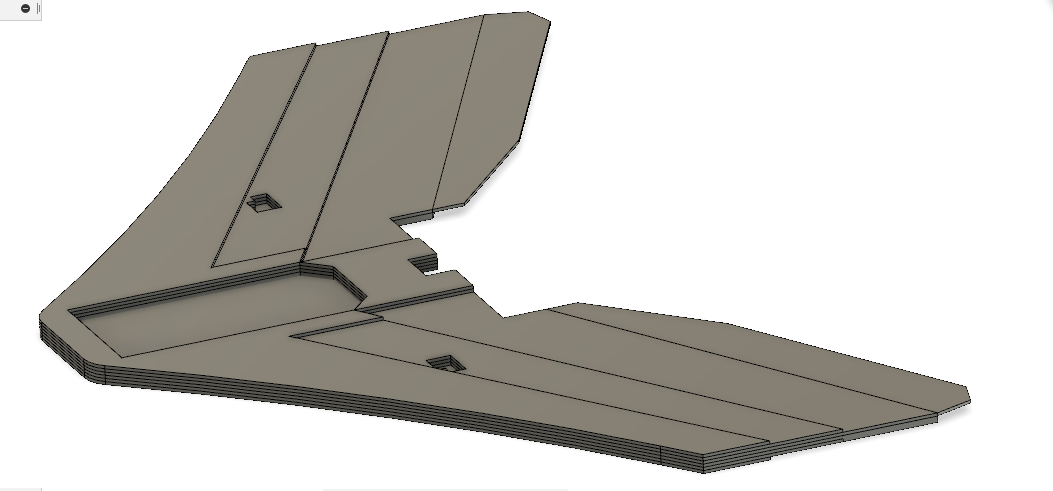
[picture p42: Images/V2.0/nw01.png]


The motor mount is designed to sequrely hold on to the layers of foam. Its a minimal design and provides resonable sturdiness when attached to the foam.

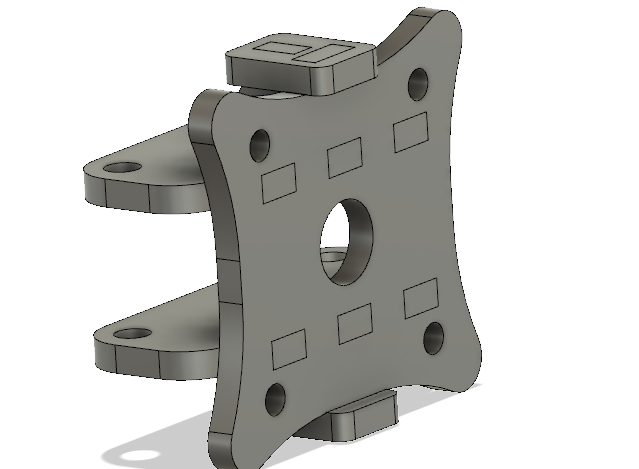
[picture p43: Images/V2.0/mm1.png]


The two locking clips on the top and bottom, provides assurance that the motor plate won't come loose from the assembly. The entire part is covered in a syntetic resin to provide strength and resist vibration.

The 3D model is converted into **DXF** format and made sutitable for CNC cutting. The design is cut on **Shopbot PRS alpha 3-axis CNC mill** using the [CNC Drag knife](https://github.com/rahulsarchive/cncdragknife) we designed. 

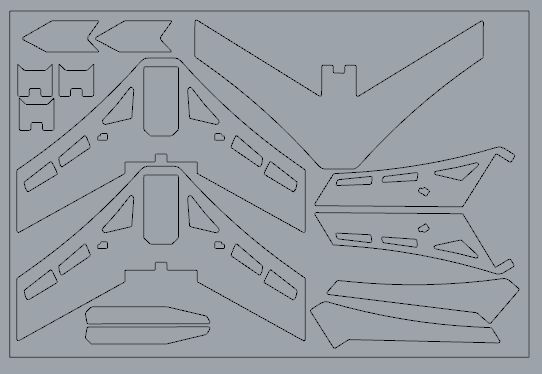
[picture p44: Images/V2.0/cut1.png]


We did not have depron foam available with us, so we decided to use **Coroplast** for the construction. It's heavier than depron but is also much stronger, it can take impact well and binds well with hotglue and syntetic rubber adhesives.

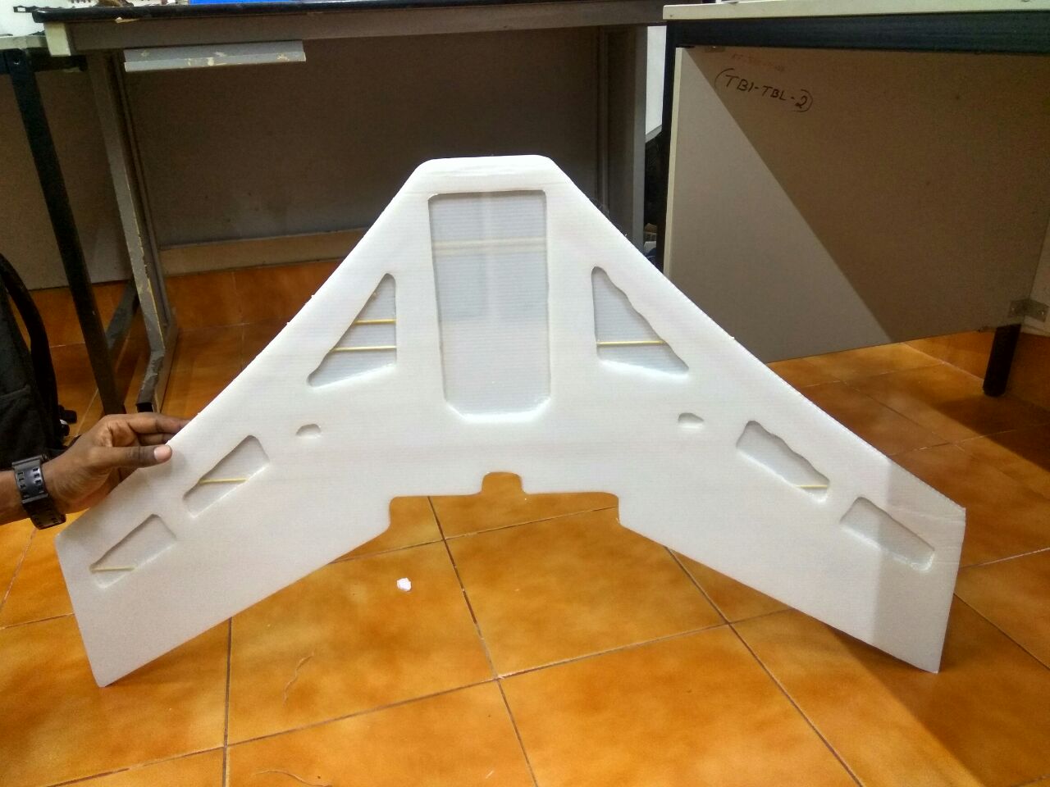
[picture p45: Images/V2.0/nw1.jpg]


The final assembly with all the layers stuck together.

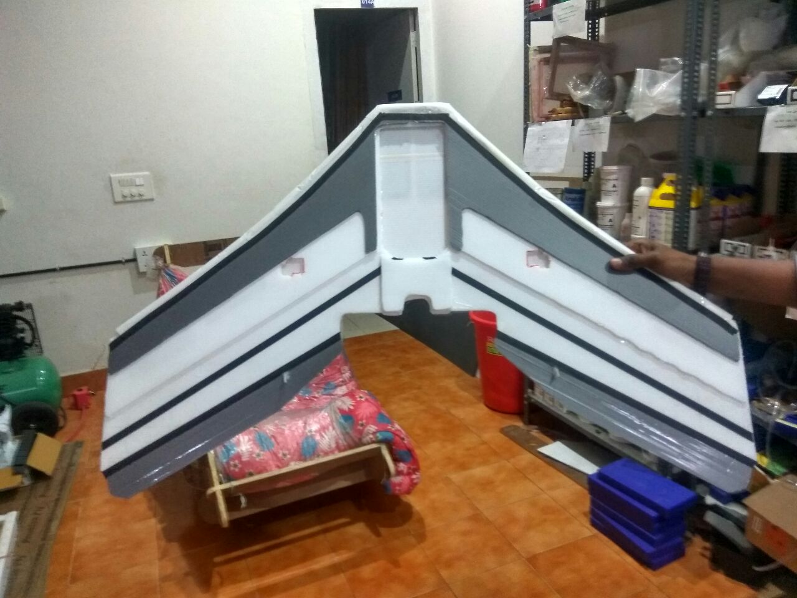
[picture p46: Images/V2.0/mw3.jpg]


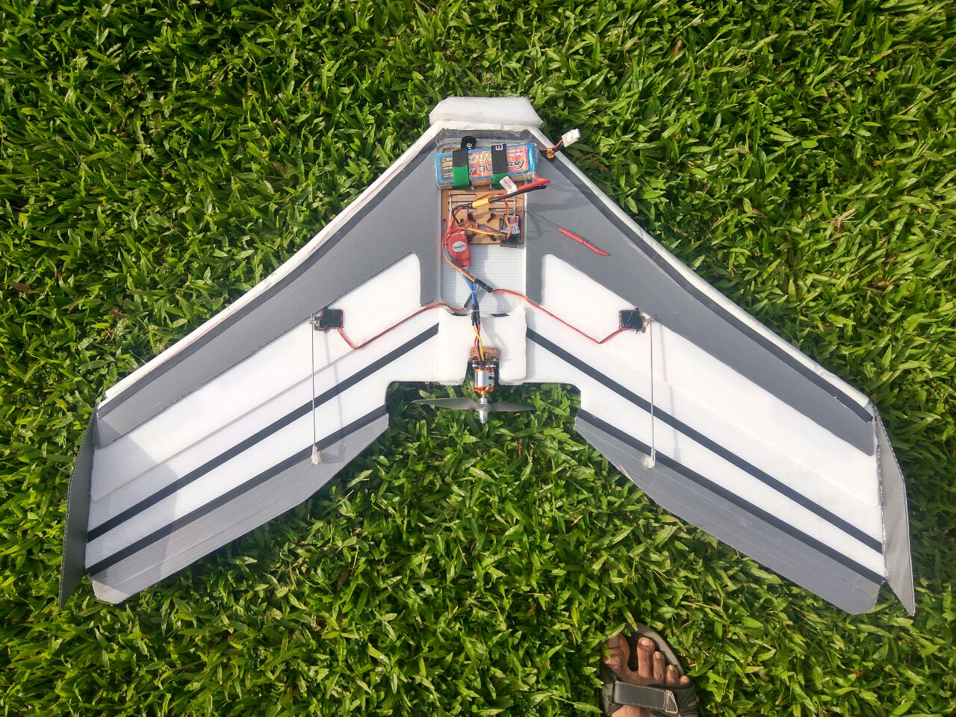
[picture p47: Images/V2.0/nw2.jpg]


The maiden went beautifully, the KFm performed well, the wing resisted tip stalling and glides like its on rails.Because of the sweep, the COG balances prefectly with a 3800mah 3S lipo. Takes off at about 70% throttle and cruises at 50%. Since we used coroplast, the wing is a bit heavy for a 1m wing span model, as such needs to fly a bit faster to maintain altitude. 

The wing loading on the plane is a bit higher with an area of 28dm^2 and AUW of 1200g. This needs an expert level of control to keep the craft in the air.

### Note

1. Sweep provides dihedral stability and COG leverage.
2. Coroplast is heavier, when desigining a model, built it at 1.5 times scale.
3. 1m wingspan and 28dm^2 wing area is not enough for a 1.2kg model. Wing cube loading puts it in the acrobatic range.
4. choose a motor with a thrust greater than the weight of the model.

## Version 2.1 (TomCat, KFM4 Wing)

Wingspan: 1200mmm   
Sweep: 35 deg  
Root chord: 320mm
Tip chord: 260mm
AUW: 1000g  
Power plant: 2826 1500kv motor (9X6 prop) 

We decided to built a bigger and lighter version of the wing, it will have lighter wing loading and can fly more slowly.

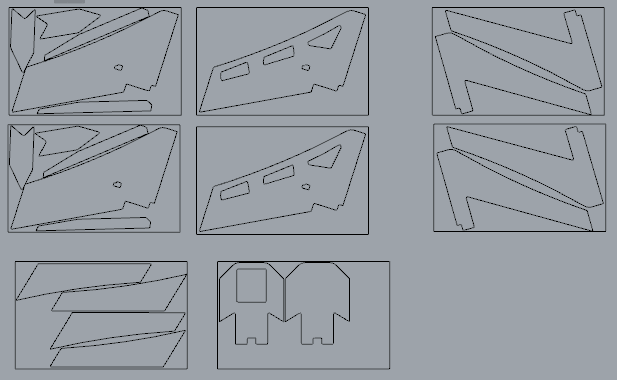
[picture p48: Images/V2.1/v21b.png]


The wing is made from **5mm depron** sheets, depron is much more easier to work with than coroplast. It is lighter and can be bend when heated. The wing is made by stacking 4 layers of depron sheets to from the KFm4 airfoil.
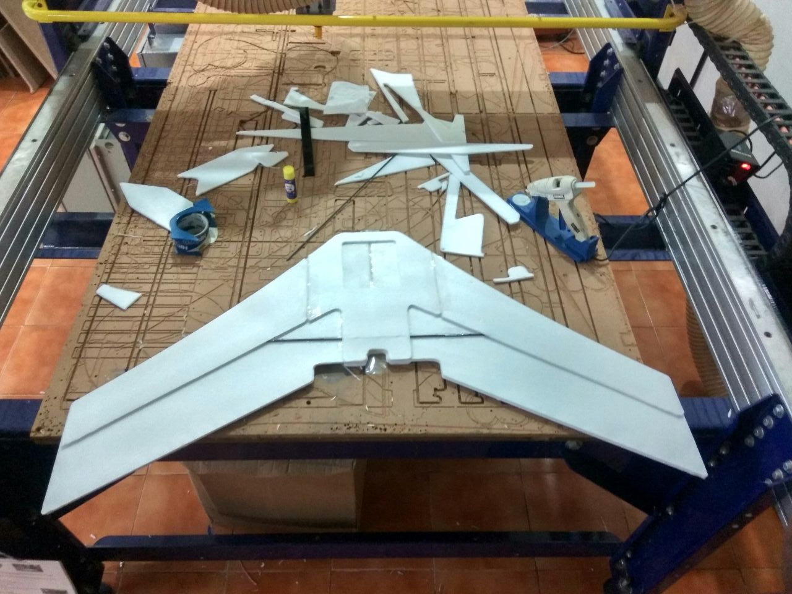
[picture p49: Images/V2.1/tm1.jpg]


The layers are stuck together with hotglue and syntetic resin. There is thin laminating layer on the depron which provides strength, if you remove the layer by sanding, it will weaken the structure.

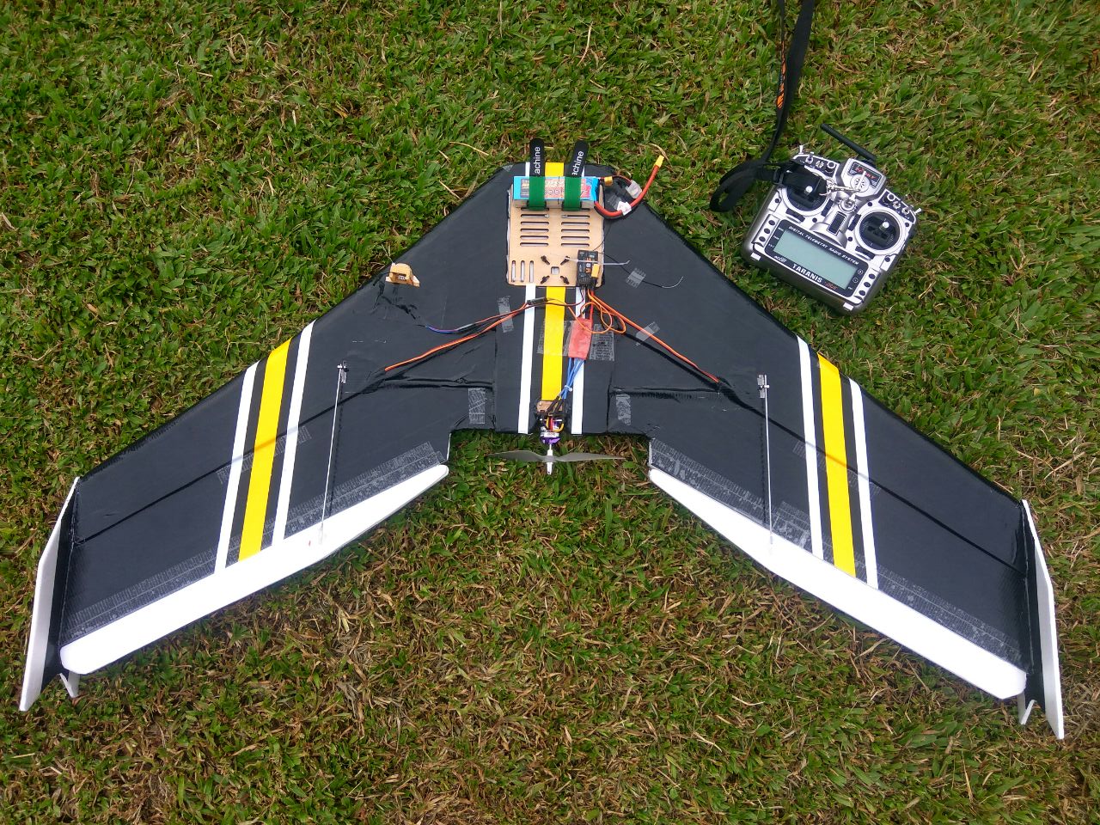
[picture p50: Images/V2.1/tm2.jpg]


We laminated the wing with black packing tape. The tape provides the strenght for the model, we used a thicker tape and the weight of the model increased by 100g. Light weight packing tape would be a better choice.

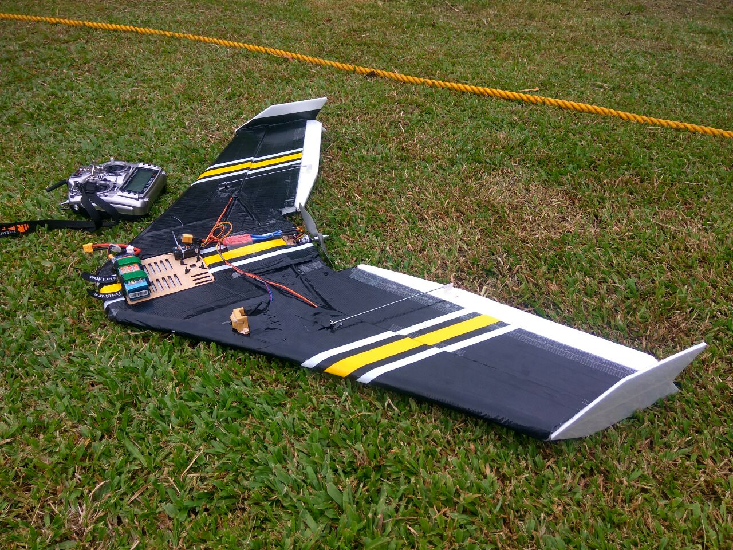
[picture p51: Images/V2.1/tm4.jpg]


The stripes are added for effect. It does make the wing look cool.

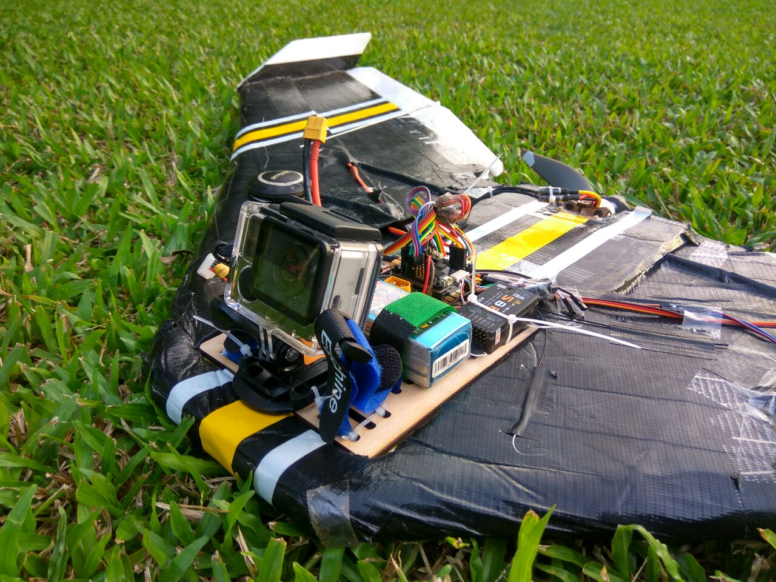
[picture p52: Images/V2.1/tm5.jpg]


The wing flies beautifully, it glides forever. Very good slow flying characteristics and controllability. When flying slow wind does push the craft around, buut once you get some speed it flies like an arrow. Very little relex on the elevons was need to keep it level.

### Note

1. Don't be afraid of building bigger wings, they have far more stable and have good slow flying characteristics.
2. Hot glue is heavy, use it sparingly.
3. Depron bonds well with polyurethane glue, for lighter build, can use ordinary glue stick.
4. Built elevons a bit bigger to increase responsiveness at slow speeds.

### Version 3.0 (OrangeFury)

Wingspan: 1400mmm   
Sweep: 30 deg  
Root chord: 380mm
Tip chord: 220mm
AUW: 1500g  
Power plant: 3530 1400kv motor (9X6 prop) 

This will be a slightly bigger wing than the previous one, we want it to carry a downward facing camera for arieal mapping purposes. 

open uav

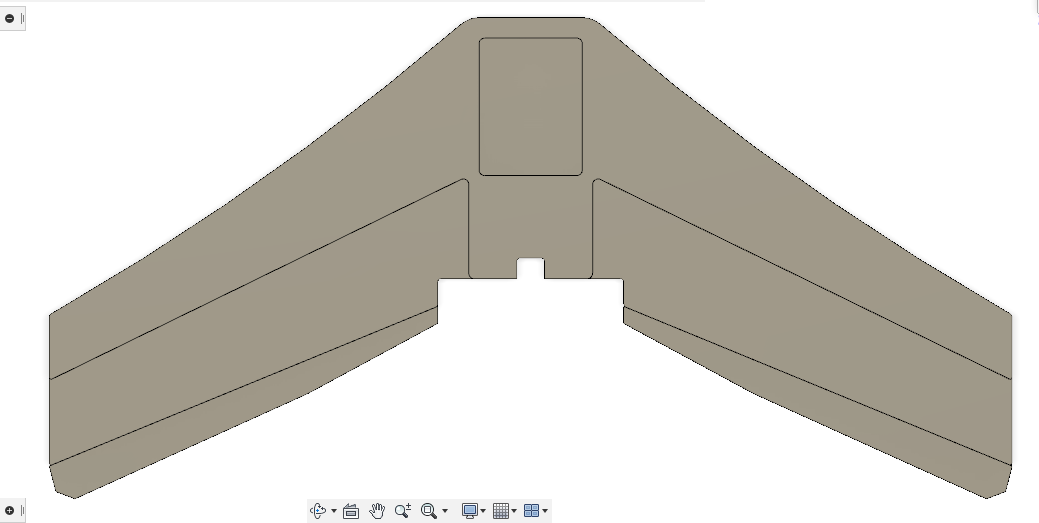
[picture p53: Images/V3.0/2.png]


It will be a heavier version witha slighly longer wingspan and reduced sweep angle to bring the CG forward as we will be putting a 6000mah (2X3S) battery and Gopro in the front.

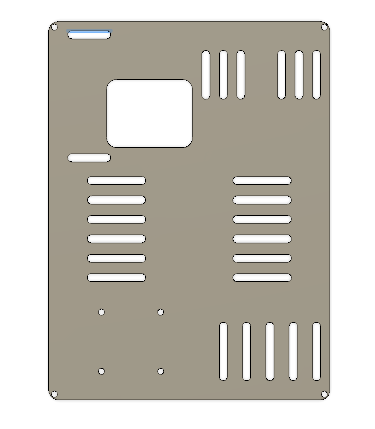
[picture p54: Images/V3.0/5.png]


The battery plate with the provisons for attaching two Gopro cameras, one facing downwards and other facing forwards. It will support 2X 2600 mah batteries, a flght controller and receiver.

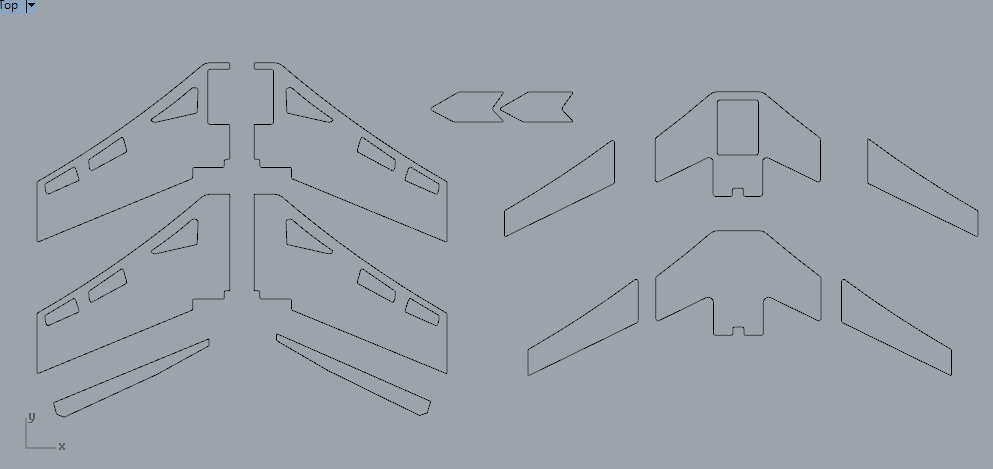
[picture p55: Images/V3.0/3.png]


The design made ready for cutting in the CNC machine using a Drag Knife. 

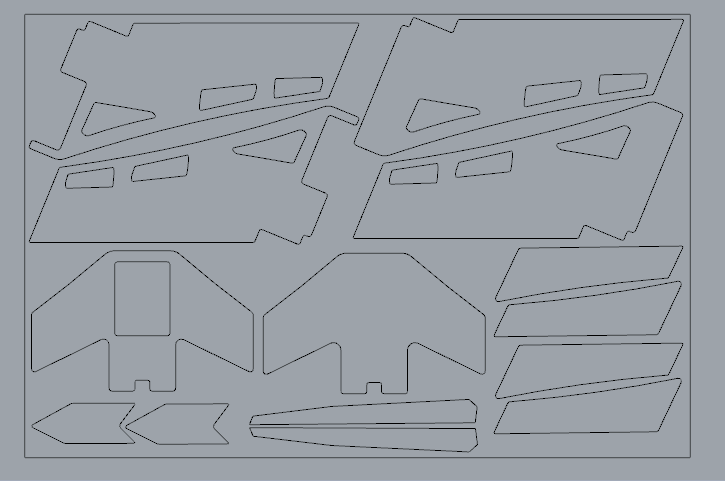
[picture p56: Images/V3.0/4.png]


The parts are split apart and arranged to provide the most economical use of material and provide strength where needed and reduce weight were not needed.

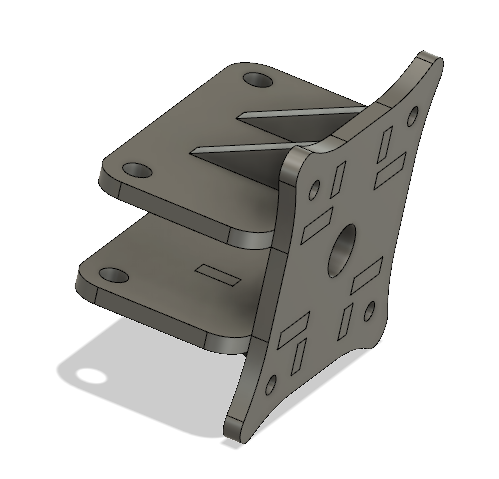
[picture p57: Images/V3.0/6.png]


The motor plate with the larger base and  stronger supports for the bigger motor.

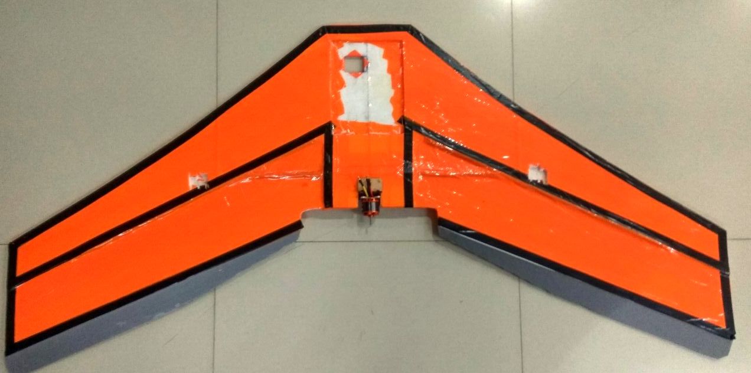
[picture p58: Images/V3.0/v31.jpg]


The wing is fitted with the MatekF405 flight controller, an Frsky S8r radio, SIK radio telemetry, Skywalker 60A ESC, DYS 3536 1100Kv motor

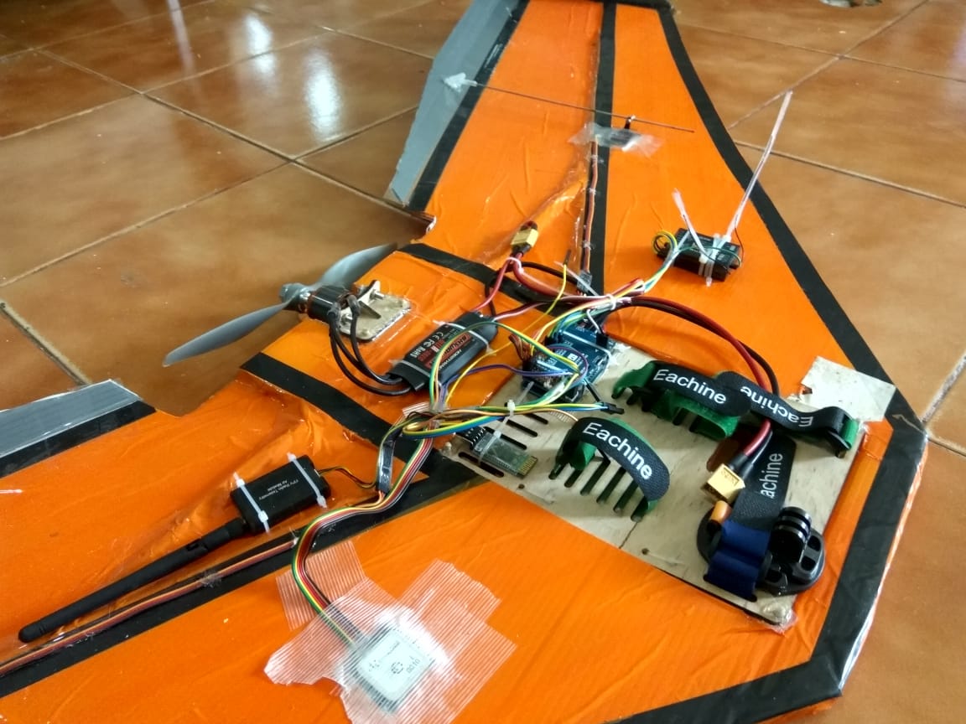
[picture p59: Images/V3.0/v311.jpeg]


The wing was big and heavy, but the material choice was poor, the coroplast was sagging at the ends, the frame as a whole is not rigid enough and the flight chracteristics were not as good as expected, its a bit tail heavy.

### Note

1. Coroplast is not suited for bigger wingspan.
2. The sweep angle was too shallow, and the plane became tail-heavy.
3. Airfoil benefits of KFm4 were missing, it behaved like a plank.

## Version 4.0 (Stingray, KFM6)

Wingspan: 1250mmm   
Sweep: 30 deg  
Root chord: 380mm
Tip chord: 220mm
AUW: 1300g  
Power plant: 3530 1400kv motor (9X6 prop) 

Considering all the things we learned from the previous model we decided to build a new model with some modifications like, switching from to a KFm6 airfoil and building the plane out of 5mm Depron, which is much lighter.

Cutting Depron in Shopbot CNC mill. The frame is made form multiple sheets stacked on top.

open uav

The arrangement showing how the pieces fit together.

open uav

The model after assembling.

open uav

Finishes sticking all the parts together and made a fuselage out of depron for housing all the electronics.

open uav

The Elevons sanded to give the airfoil shape. and attached to body uing Nylon hinges.

open uav

The finished airframe with a painted body and tape covering to protect it from damage.

open uav

The wing flies well, it needs a 5000mah battery and a Gopro in front to balance out the CG but once its balanced, it flies well, good glide slope and stall characteristics. The KFm6 seems to work well with this airframe.

open uav

## Resources

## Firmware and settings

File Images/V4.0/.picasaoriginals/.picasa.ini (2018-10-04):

[v4.jpeg]
filters=crop64=1,721098ffffe341;enhance=1;autolight=1;finetune2=1,0.508772,0.000000,0.084211,00000000,0.274854;
crop=rect64(721098ffffe341)
moddate=f3ffeec0ca5bd401
width=1152
height=864
textactive=0
[1.jpeg]
filters=crop64=1,138e04e4e4bdffff;autolight=1;autocolor=1;
crop=rect64(138e04e4e4bdffff)
rotate=rotate(3)
moddate=e8988cd5cd5bd401
width=864
height=1152
textactive=0
[2.jpeg]
filters=tilt=1,0.130390,0.000000;crop64=1,1f680000d2aafae3;autolight=1;autocolor=1;
crop=rect64(1f680000d2aafae3)
rotate=rotate(3)
moddate=289f0c00ce5bd401
width=864
height=1152
textactive=0
